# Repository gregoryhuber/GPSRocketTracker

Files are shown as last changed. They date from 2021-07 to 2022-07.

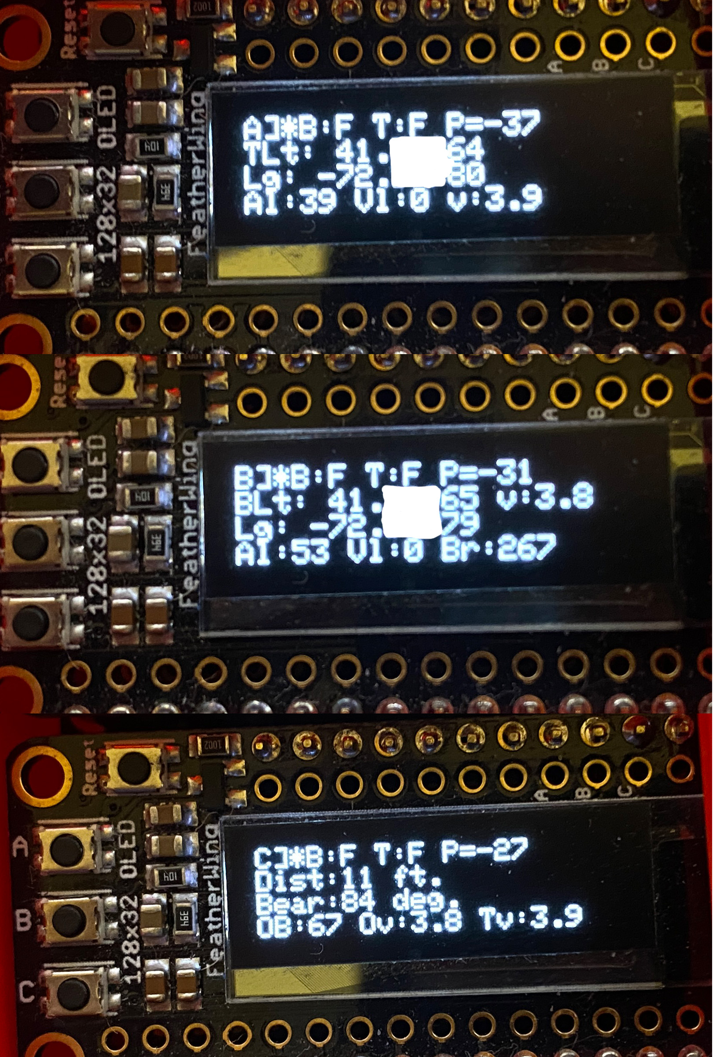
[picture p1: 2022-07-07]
Photos/DisplayScreenExamples.jpg

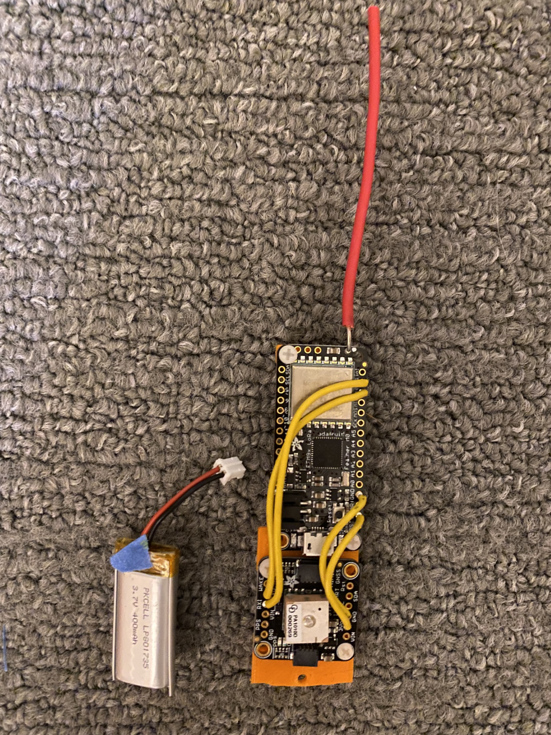
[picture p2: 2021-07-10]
Photos/Transmitter_Front.jpg

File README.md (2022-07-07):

https://github.com/gregoryhuber/GPSRocketTracker

This is the repository for a homebrew GPS Rocket Tracker built around Arduino feather M0 units with embedded LORA radios. Observed successful range over flat territory (when the rocket is laying on the ground) is 1.2km. Longer range has been achieved when the target is airborne, but I'm not sure yet what the maximum is. It likely depends on the antenna.

Comments/improvements/etc. welcome. Please email:

gregory.a.huber@outlook.com with the subject "Arduino Lora Tracker"

==============================

This project requires two units:
(1) A transmitter, the unit that goes in the rocket, which sends its GPS information every second
(2) A receiver/base unit, which you hold onto, which tracks its own GPS location, receives information from the transmitter, and can route you to the transmitter in certain configurations.

Manifest:

Parts lists for each unit, available from AdaFruit, are in the PartsList folder

Shape files (stls) are in the STLfiles folder. There are separate folders for the case that holds the receiver/base unit and transmitter in the two stacked vertical feathers orientation that fits in a 24mm body tube.

Photos of the assembled transmitter and receiver are in the Photos folder.

(Note that there are not photos of the transmitter with an SD Card unit included, but that you can use an SD card on the transmitter.)

Code: 

Recevier.ino in the folder "Receiver" is the code for the receiver/base unit.

Transmitter.ino in the folder "Transmitter" is the code for the transmitter unit.

==============================

Brief overview of code edits/decisions:

The transmitter and receiver need to share a frequency (probably 915mhz, but in the US it can be anything in the range of 902 to 928 MHz if your hardware supports it. See https://www.everythingrf.com/community/lora-frequency-bands-in-north-america) and a 3 digit "MagicNumber." The 3 digit code allows the receiver to know what unit it should be talking to.

See these lines in both files:
#define RF95_FREQ 915.00
#define MagicNumber 123
*** You must set the Mhz and MagicNumber to be the same between your transmitter and receiver units, and should change them from the defaults so you don't conflict with someone else. Even with different codes, units operating on the same frequency may conflict.

You upload the relevant code, using the Arduino IDE, to both the transmitter and the receiver/base unit. 

In the TRANSMITTER codebase, you have to set three flags:

#define UseRadio true
Only turn this to false if you just want to display or capture to the SD Card GPS data0

#define UseSDCardWriter false
You can turn this to true if you install an SD card module and want to record/log data to it.

#define UseDisplay false
Only turn this to true if you have a display installed and you want the transmitter to display its own address.

In the RECEIVER codebase, you have to set two flags

#define UseDisplay true
If you don't have a display (and are only teathered to a PC) you can set to false.

#define PrintDataToSerialForLogging true
This outputs the data received to the serial port, so you can plot it or save it in real time.

PLEASE NOTE: There are also numerous debugging flags in the code, which you can use to diagnose problems (like bad wiring to the GPS or SDCard module/etc.). Leave them as FALSE unless you need to fix things. If you leave them on and try to record data from the receiver on a PC it will screw up the data stream.

==============================

Details about functionality

The receiver has three information screens, selected by pressing the top (A), middle (B), or bottom (C) button on the display.

Screen A displays information about the transmitter.
Screen B displays information about the base station.
Screen C is a navigation screen that guides you from the base to the transmitter.

On all three screens, the top row is the same:

{A,B,C}]*B:XX T:XX P=XX
Where A/B/C is which screen you are on.
The * appears whenever a new packet is received from the transmitter
B: XX indicates the status of the base's GPS fix: F=Valid current Fix;SF(#)=Stale fix, # of seconds since last valid GPS Fix;NF=Never had a valid GPS Fix
T: XX indicates the status of the transmitter's GPS fix: F=Valid current Fix;SF(#)=Stale fix, # of seconds since last valid GPS Fix;NF=Never had a valid GPS Fix;NS Never synced with transmitter
P = XX is the signal strength/RSSI, if synced, of last packed received from transmitter

On Screen A, the next rows will display a summary of the TRANSMITTER's GPS data:
Never Target Sync
or
Never Target Fix + the Transmitter's read battery voltage
or
Lat, Long, Altitude (in meters), Velocity (MPH)+ the Transmitter's read battery voltage

On Screen B, the next rows will display a summary of the BASE's GPS data:
Never Target Fix + the BASE's read battery voltage
or
Lat, Long, Altitude (in meters), Velocity (MPH), Bearing (Degrees) + the Transmitter's read battery voltage

On Screen C, the next rows display
"Can't navigate. Missing something." if either the TRANSMITTER or BASE GPS is missing
or
Distance (feet) and Bearing (degrees) from the BASE to the transmitter
Plus Own bearing, Own Battery Voltage, and Transmitter Battery Voltage

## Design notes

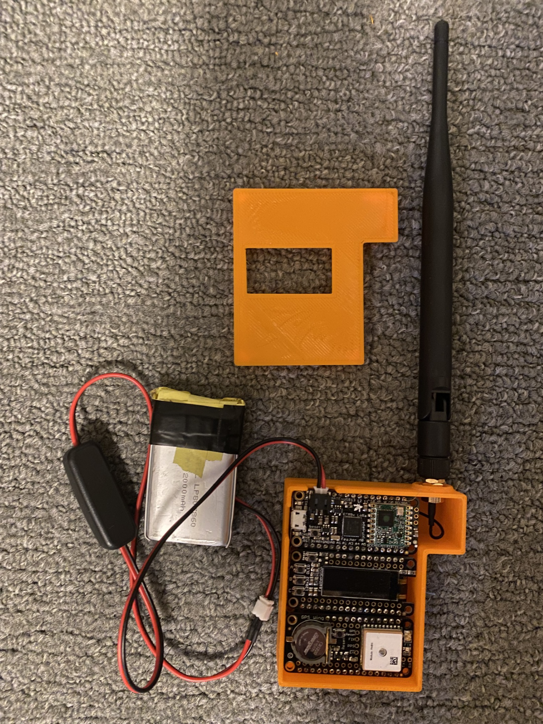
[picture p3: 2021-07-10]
Photos/BaseUnitInCase.jpg

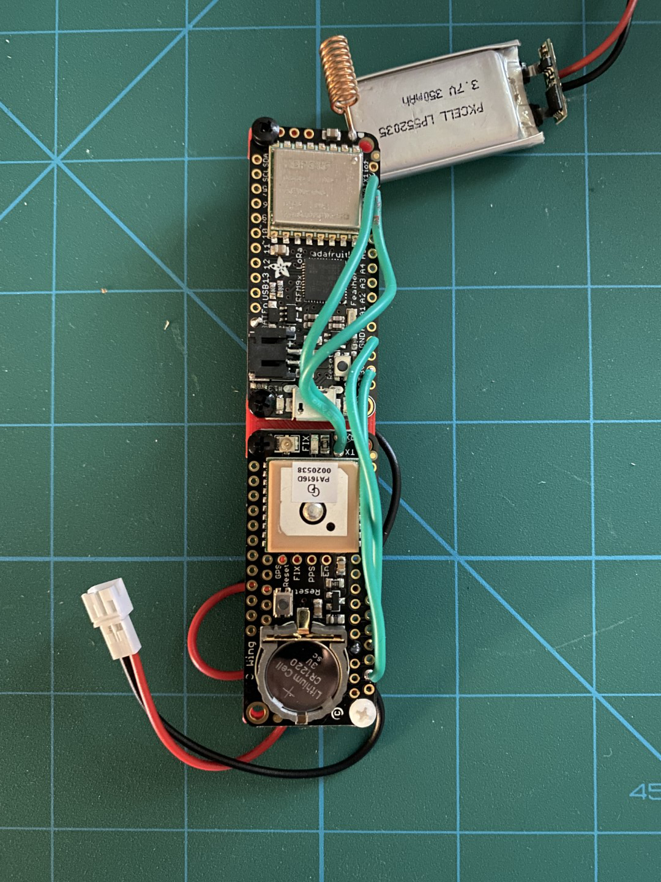
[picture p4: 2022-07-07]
Photos/Transmitter_Narrow_Front.jpg

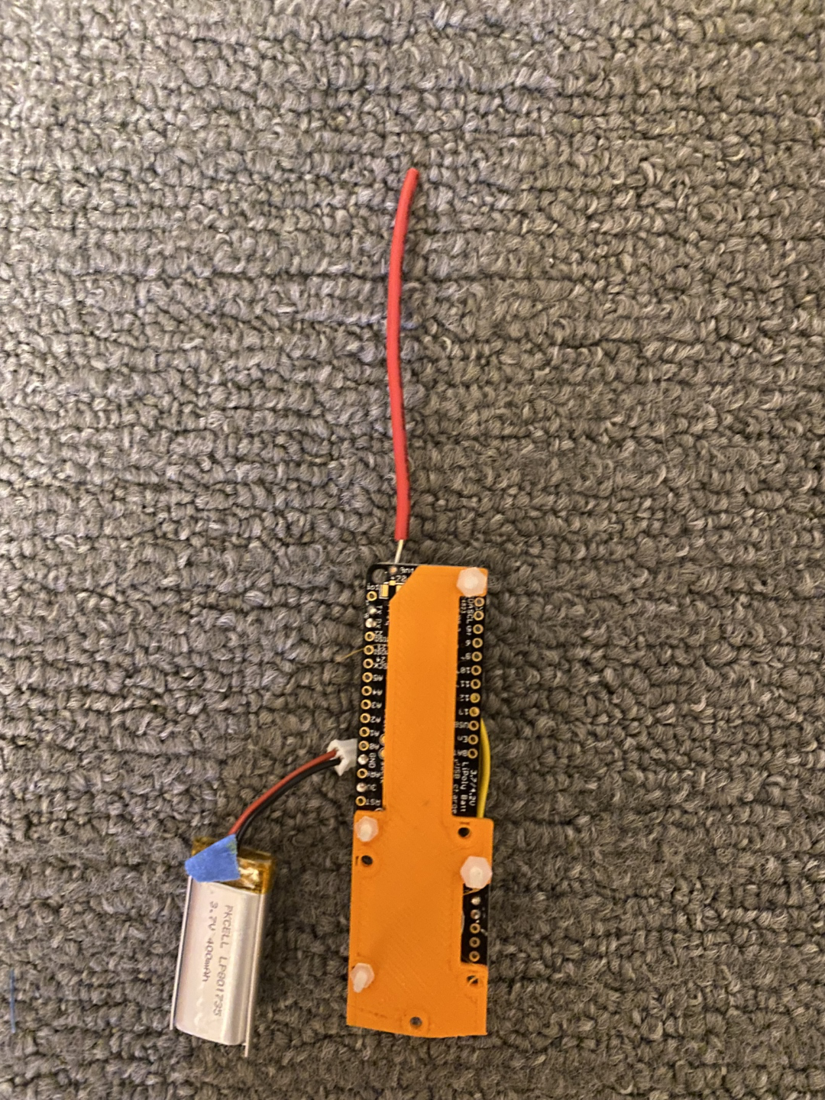
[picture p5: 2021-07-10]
Photos/Transmitter_Rear.jpg

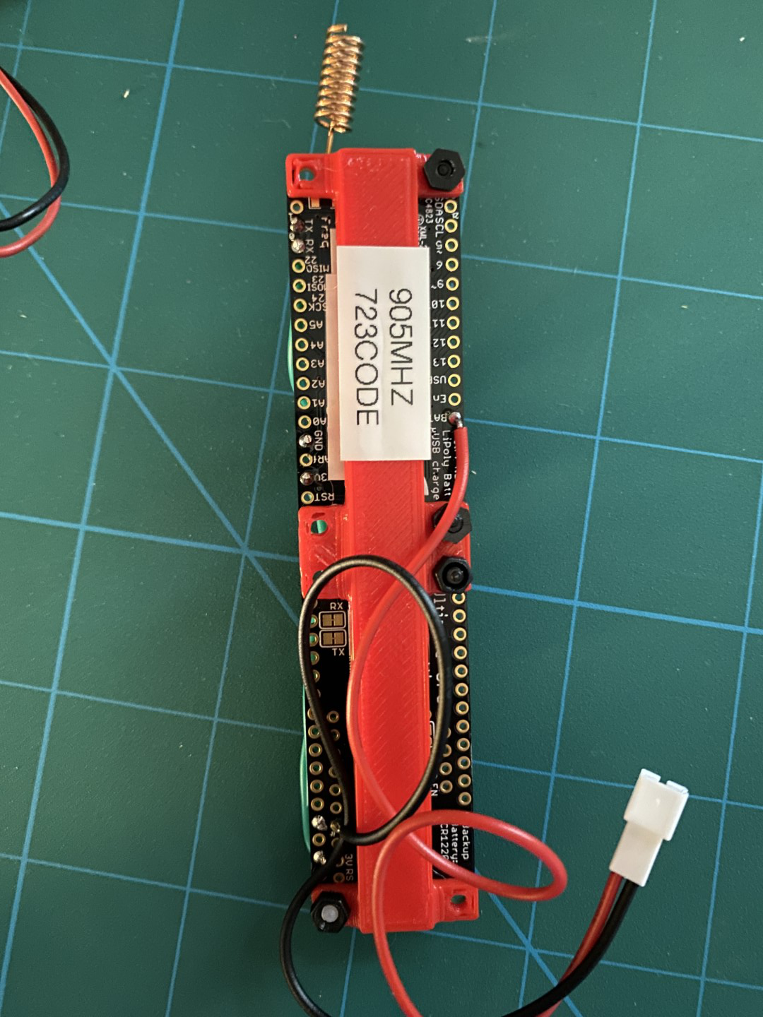
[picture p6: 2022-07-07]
Photos/Transmitter_Narrow_Back.jpg

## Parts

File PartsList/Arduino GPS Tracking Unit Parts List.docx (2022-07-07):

Receiver (Complete Unit with coil antenna $100.25)

FeatherWing Triple (base unit) $8.50

https://www.adafruit.com/product/3417

Adafruit Feather M0 with RFM95 LoRa Radio - 900MHz – RadioFruit $34.95

https://www.adafruit.com/product/3178

Adafruit Featherwing GPS receiver $24.95

https://www.adafruit.com/product/3133

Adafruit Featherwing Display Unit/Control Buttons (with headers) $15.95

https://www.adafruit.com/product/3045

Large battery $14.95

https://www.adafruit.com/product/328

Antenna Options:

Simple Spring (coil) Antenna $.95

https://www.adafruit.com/product/4269

OR

uFL SMT Connector $.75

https://www.adafruit.com/product/1661

900 Mhz Antenna $12.75

https://www.adafruit.com/product/3340

Optional:

Battery patch cable with switch $2.95

https://www.adafruit.com/product/3064

3D Printed Case for Base Unit

With Spring Antenna:

With large antenna:

See BaseUnitBottomOfCase.stl and BaseUnitTopOfCase.stl

Transmitting Unit ($66.85)

Adafruit Feather M0 with RFM95 LoRa Radio - 900MHz – RadioFruit $34.95

https://www.adafruit.com/product/3178

GPS receiver

Option 1, smaller: $29.95

https://www.adafruit.com/product/746

Option 2, feather: $24.95

https://www.adafruit.com/product/3133

400mah LIPO battery $6.95

https://www.adafruit.com/product/3898

Quarter Wavelength Wire antenna (3.12inches) (free)

http://www.csgnetwork.com/antennagenericfreqlencalc.html

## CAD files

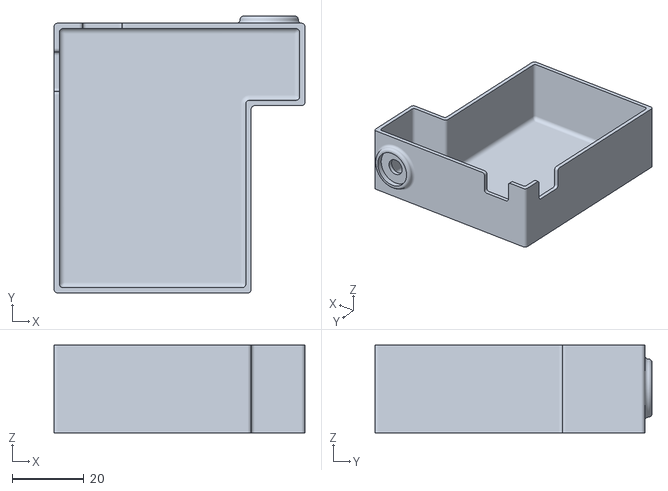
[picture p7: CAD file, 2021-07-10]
STLFiles/BaseUnitCase/BaseUnitBottomOfCase.stl
70.0 x 77.2 x 24.5

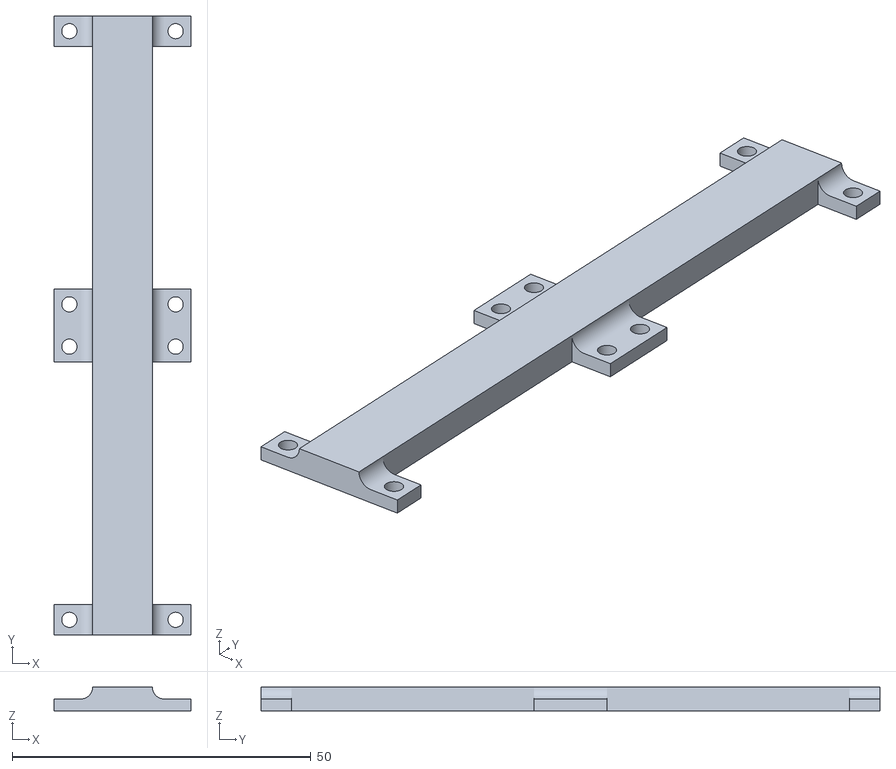
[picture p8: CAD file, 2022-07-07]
STLFiles/VerticalFeathers24MMTube/VerticalFeathers24MMTube.stl
22.9 x 103.6 x 4.00

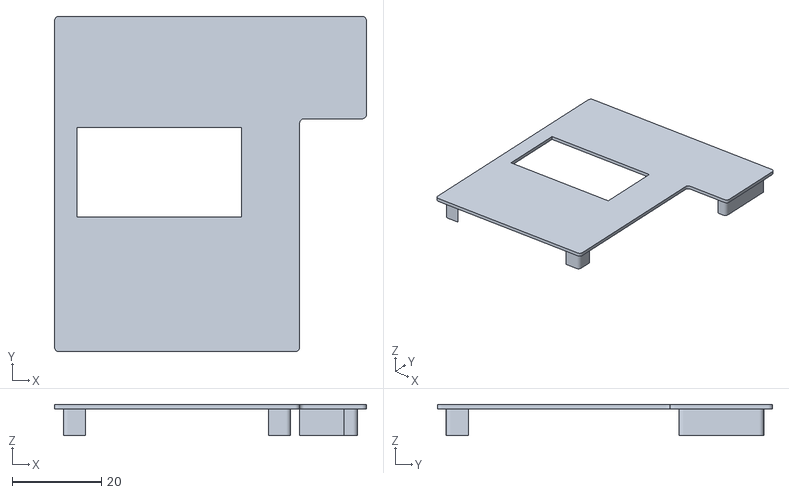
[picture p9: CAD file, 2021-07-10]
STLFiles/BaseUnitCase/BaseUnitTopOfCase.stl
70.0 x 75.2 x 7.00

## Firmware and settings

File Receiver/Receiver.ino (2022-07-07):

//////////////////////////////////////////////////////////////////////////
// RFM95 Lora Arduino GPS tracking system
// Version 2.1
// 2022/07/01
// Gregory Huber (gregory.a.huber@outlook.com)
//
// This is the code for the RECEIVER
//
//////////////////////////////////////////////////////////////////////////

// This is the receiver half of the codebase for an Arduino feather-based GPS tracking system suitable for rocket tracking
// The physical setup is comprised of a base station (receiver) and a tracker (transmitter)

// The base station is built around the following minimal equipment:
// Adafruit Feather M0 with RFM95 LoRa Radio - 900MHz – RadioFruit https://www.adafruit.com/product/3178

// The following parts are optional if you just want to capture data from the transmitter directly to a PC

// Necessary to dispay incoming GPS data and to use free navigation (without connection to a PC)
// Feather Display Unit/Control Buttons (with headers) https://www.adafruit.com/product/3045
// Set UseDisplay below to true to use

// Necessary to use free navigation (without connection to a PC)
// Feather GPS receiver https://www.adafruit.com/product/3133
// Even if no GPS is present, code will still run

// These are hardware options to hold everything as well as a good antenna option. I find soldering the uFL connector hard so I tend to use simple wire antennas
// FeatherWing Triple (base unit) https://www.adafruit.com/product/3417  
// uFL SMT Connector https://www.adafruit.com/product/1661
// 900 Mhz Antenna https://www.adafruit.com/product/3340
// 2000mAh LIPO battery https://www.adafruit.com/product/2011

// This code draws on the following resouces and references. Thank you.
// This is a fully fleshed out example from which many of the transmission details were copied https://github.com/mloudon/electrosew/blob/master/feather_send/feather_send.ino
// https://gis.stackexchange.com/questions/252672/calculate-bearing-between-two-decimal-gps-coordinates-arduino-c
// https://community.particle.io/t/tinygps-using-distancebetween/28233/3
// http://www.airspayce.com/mikem/arduino/RadioHead/classRH__RF95.html
// https://www.thethingsnetwork.org/forum/t/best-practices-when-sending-gps-location-data/1242/40

// Version 2.5 (2022/07):
// Introduced data structures, which allowed much more efficiently sending more data in the LORA packet
// On the transmitter:
    // Read and send battery voltage
    // Added support for a data logger
    // Refined display code to fix what is displayed on transmitter
// On the receiver/base unit:
    // Implement serial logging to connect to PC
    // Improve option for running without display
    // Read and display battery voltages
    // Improved handling of stale packets/stale GPS data
    // More data/info now displayed on screen

#include <Adafruit_GPS.h>
#include <math.h>;
#include <SPI.h>
#include <Wire.h>
#include <Adafruit_GFX.h>
#include <Adafruit_SSD1306.h>
#include <RH_RF95.h>

////////////////////////////////////////////////////////////////////////////////////////////
//
// Radio constants
//
////////////////////////////////////////////////////////////////////////////////////////////
  
  // This is important. This defines the frequency the units will use. Both base and transmitter need to be on the same frequency
  // LORA frequency range in the US is 902 to 928 MHz https://www.everythingrf.com/community/lora-frequency-bands-in-north-america
  // I do not not know if you can provide more specificity here (say 915.2)
  #define RF95_FREQ 915
  
  // The magic number is a unique three digit code that is used to verify the pair between tracker and base unit.
  // Valid ranges are 000 to 999
  // If these numbers don't match, any incoming packet is ignored
  // Please change it to something different form this so that your tracker doesn't conflict with someone else's!
  #define MagicNumber 123

////////////////////////////////////////////////////////////////////////////////////////////
//
// Hardware setup options
//
////////////////////////////////////////////////////////////////////////////////////////////

  #define UseDisplay true

////////////////////////////////////////////////////////////////////////////////////////////
//
// Connection to PC options
//
////////////////////////////////////////////////////////////////////////////////////////////

  // For real time-tracking using PC, enable printing of target GPS to serial port for plotting
  #define PrintDataToSerialForLogging true
  // Note that if this is enabled, other debugging flags below should be set to false 
  // or else reading serial port will likely crash

////////////////////////////////////////////////////////////////////////////////////////////
//
// Timing constants
//
////////////////////////////////////////////////////////////////////////////////////////////

  // Update intervals for getting own GPS locations
  // These are in milliseconds, so 1000 = 1 second
  #define OwnGPSUpdateInterval 500
  #define DisplayUpdateInterval 250
  #define ButtonUpdateInterval 500
  #define SerialPortUpdateInterval 500

////////////////////////////////////////////////////////////////////////////////////////////
//
// Debugging
//
////////////////////////////////////////////////////////////////////////////////////////////

  // Enable each of these flags to enable diffent parts of the DebugDebugging code
  #define DebuggingOwnGPS false        // DebuggingOwnGPS prints to serial own gps data
  #define DebuggingIncoming false      // DebuggingIncoming prints to serial the incoming packet data
  #define DebuggingOwnRadio false      // DebuggingOwnRadio prints to serial configuration for the LORA radio

  // Fake data used for static GPS testing
  // Lat/Long is the New Haven, CT Green. Other data is made up.
  #define UseStaticData false
  #define StaticLat 41.308231
  #define StaticLong -72.926173
  #define StaticBearing 317
  #define StaticVelocity 987
  #define StaticAlt 3611
  #define StaticNumSatelites 8
  #define StaticSecondsSinceUpdate 27
  #define StaticEverValidFix 1
  #define StaticVBAT 4.10  

////////////////////////////////////////////////////////////////////////////////////////////
//
// Define pins/hardware
//
////////////////////////////////////////////////////////////////////////////////////////////

  //////////////////////////////////////////////////////////////////////////////////////////
  // Battery voltage
  // Battery voltage is measured on A7 on the M0
  #define VBATPIN A7

  //////////////////////////////////////////////////////////////////////////////////////////
  // GPS
  // hardware serial port for the GPS
  #define GPSSerial Serial1

  // Connect to the GPS on the hardware port
  Adafruit_GPS GPS(&GPSSerial);

  //////////////////////////////////////////////////////////
  // Setup OLED display
  Adafruit_SSD1306 display = Adafruit_SSD1306(128, 32, &Wire);
      
  // OLED FeatherWing buttons map to different pins depending on board:
  #define BUTTON_A  9
  #define BUTTON_B  6
  #define BUTTON_C  5

  //////////////////////////////////////////////////////////////////////////////////////////
  // Setup LORA Radio
  #define LED           13
  #define RFM95_CS      8
  #define RFM95_INT     3
  #define RFM95_RST     4

  // Create singleton instance of the radio driver
  RH_RF95 rf95(RFM95_CS, RFM95_INT);

////////////////////////////////////////////////////////////////////////////////////////////
//
// Structures
//
////////////////////////////////////////////////////////////////////////////////////////////

  // uint8_t is 0 to 255
  // uint16_t is 0 to 65535 
  // uint32_t 0 to 4,294,967,295
  
  // This is the structure we use to store our own GPS data at all times
  struct __attribute__ ((packed)) processed_gps_t {
    bool evervalidfix;              // whether we've ever had a valid gps fix
    uint32_t lastupdatemillis;      // last gps update in millis format
    uint32_t lastupdatetime;        // last gps update in hhmmss integer format
    uint32_t secondsincelastupdate; // last gps update in millis format
    bool stalelocation;             // whether last gps update was more than 60 seconds ago (1=yes)
    
    int numsatellites;              // number of satellites in last fix
  
    double latitude;          // in decimal format
    double longitude;         // in decimal format
    int32_t altitude_meters;  // in meters
    uint32_t velocity_mph;    // in mph
    uint16_t  bearing;        // in degrees (0-360)
    
    double bvolt;             // battery voltage [Range 3.0 to 4.2]
  } ;
  
  // declaring a new type "radiopacket_gps_t" as a structure for the info we want to send/receive
  // there is a fair bit of being creative here to keep the packet as small as is possible
  struct __attribute__ ((packed)) radiopacket_gps_t {
  
    //This is 2-bit unsigned integer, which ranges from 0 to 65535 
    uint16_t vbat_code;               // 2 digits are vbat * 10 and 3 digits are unique code for pairing
    
    //Thse are 4-bit unsigned integers, which ranges in value from 0 to 4,294,967,295 = 10 digits to play with
    //With 5 digits of decimal precision we still have two additional place for storing other data
    uint32_t bear_veloc_alt;          // format is XXX bearing, XXX velocity capped at 999, and XXXX altitude in meters +100 capped at 9999
    uint32_t latitude_sats_ever;      // lat with +180 to ensure positive and 5 digits precision uses 8 digits, 1 digit for # satellites seen, 1 digit for whether ever valid fix
    uint32_t longitude_sincelastfix;  // long with +180 to ensure positive and 5 digits precision uses 8 digits, 2 digits for seconds since last fix, capped at 99
  } ;
  
////////////////////////////////////////////////////////////////////////////////////////////
//
// Globabl Variables
//
////////////////////////////////////////////////////////////////////////////////////////////

  // Own GPS Data
  processed_gps_t OwnGPSData = {
    .evervalidfix=0,
    .lastupdatemillis=0,
    .lastupdatetime=0,
    .secondsincelastupdate=0,
    .stalelocation=0,
    .numsatellites=0,
    .latitude=0,
    .longitude=0,
    .altitude_meters=0,
    .velocity_mph=0,
    .bearing=0,
    .bvolt=0
  };

  // Own GPS Data
  processed_gps_t TargetGPSData = {
    .evervalidfix=0,
    .lastupdatemillis=0,
    .lastupdatetime=0,
    .secondsincelastupdate=0,
    .stalelocation=0,
    .numsatellites=0,
    .latitude=0,
    .longitude=0,
    .altitude_meters=0,
    .velocity_mph=0,
    .bearing=0,
    .bvolt=0
  };

  // Radio packet to receive
  radiopacket_gps_t SentDataToProcess;

  // Whether a new valid GPS location has arrived that needs to be parsed/stored
  boolean NewValidGPSDataArrived = 0;
  boolean BaseEverValidGPS = 0;  

  // Information about Target
  boolean TargetEverSync = 0;
  boolean TargetEverValidGPS = 0;  
  boolean TargetStaleLocation = 0;
  boolean GotNewLoraPacket = 0;
  boolean DisplayNewPacketFlag = 0;
  uint16_t SecondsSinceIncomingPacket = 0;
  uint16_t SecondsSinceIncomingGPS = 0;
  
  // Last RSSI from radio
  int lastRSSI;

  // store last button pushed on diplay, default to 'A'
  char LastButtonPushed = 'A';

  // Counter for packets in logfile

  // Timers
  uint32_t LastFixFromOwnGPS = 0;         // Last millis for which we got a Valid GPS Fix
  uint32_t LastUpdateOwnGPSPacket = 0;    // Last millis at which we updated the GPS Packet
  uint32_t LastLoraPacket = 0;            // Last millis for which we got a Valid GPS Fix
  uint32_t LastDisplayUpdate = 0;         // Last millis at which display was updated.
  uint32_t LastButtonUpdate = 0;          // Last millis at which button status was updated.
  uint32_t LastSerialPortUpdate = 0;      // Last millis at which sent logging packet to serial port.
  uint32_t EndLoopMillis = 0;             // Last millis at which we finished the main loop.
                                          // Used solely to deal with looping in Millis.
 
////////////////////////////////////////////////////////////////////////////////////////////
////////////////////////////////////////////////////////////////////////////////////////////
////////////////////////////////////////////////////////////////////////////////////////////
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
void loop() {

  //////////////////////////////////////////////////////////////////////////
  // Each time through the loop, check for a LORA packet
  //
  
  // Turn on communication to LORA. Keeping it off the rest of the time stops this from interfering with other parts of code.
  digitalWrite (RFM95_CS, LOW);
  
  if (rf95.available()) {
    GotNewLoraPacket = receiveLoraPacket();
    if (GotNewLoraPacket) {
      TargetEverSync = true;
      if (TargetGPSData.evervalidfix==1) {
        TargetEverValidGPS = true;
      }
      lastRSSI = rf95.lastRssi();
      LastLoraPacket=millis();
      DisplayNewPacketFlag=true;
    }
  }
  
  // Turn off communication to LORA. Keeping it off stops this from interfering with other parts of code.
  digitalWrite (RFM95_CS, HIGH);

  //////////////////////////////////////////////////////////////////////////
  // Each time through the loop, attempt to read GPS data.
  // This code doesn't try to read from GPS unless it is available.
  // Additionally, if no new data is available, it just skips through.
  if (GPSSerial.available() > 0) {
    char c = GPS.read();
    if (GPS.newNMEAreceived()) {
      if (GPS.parse(GPS.lastNMEA())) {
        if (GPS.fix==1) {
          NewValidGPSDataArrived = 1;
          BaseEverValidGPS = 1;
          LastFixFromOwnGPS = millis();
        }
      }
    }
  }

  //////////////////////////////////////////////////////////////////////////
  // Update Own GPS calculations every OwnGPSUpdateInterval
  if ((LastUpdateOwnGPSPacket+OwnGPSUpdateInterval )<millis()) {
    LastUpdateOwnGPSPacket=millis();

    // This block of conditional code just sets the GPS data to either the fixed stata data for testing purposes or the actual GPS data
    if (UseStaticData) {
      // Fixed data for testing purpuses
      OwnGPSData.evervalidfix=StaticEverValidFix;
      OwnGPSData.lastupdatemillis=millis();
      OwnGPSData.lastupdatetime=234233;
      OwnGPSData.secondsincelastupdate=(OwnGPSData.lastupdatemillis-(millis()-(1000*StaticSecondsSinceUpdate)))/1000;
      OwnGPSData.stalelocation=(OwnGPSData.secondsincelastupdate>60);
      OwnGPSData.numsatellites=StaticNumSatelites;
      OwnGPSData.latitude=StaticLat;
      OwnGPSData.longitude=StaticLong;
      OwnGPSData.altitude_meters=StaticAlt;
      OwnGPSData.velocity_mph=StaticVelocity;
      OwnGPSData.bearing=StaticBearing;
      OwnGPSData.bvolt = StaticVBAT;
    }
    else {
      // Actual data
      OwnGPSData.bvolt = (2*3.3*analogRead(VBATPIN))/1024;
      //OwnGPSData.bvolt = 4.2;
      // NewValidGPSDataArrived: This flag lets us know if in the intervening period a new GPS packet with a valid fix has been parsed
      if (NewValidGPSDataArrived) {
        // Do this if new data has arrived
        NewValidGPSDataArrived = 0;
        OwnGPSData.evervalidfix=1;
        OwnGPSData.lastupdatemillis=LastFixFromOwnGPS;
        OwnGPSData.lastupdatetime=GPS.hour*10000+GPS.minute*100+GPS.seconds;
        OwnGPSData.secondsincelastupdate=0;
        OwnGPSData.numsatellites=(int)GPS.satellites;
        OwnGPSData.latitude=GPS.latitudeDegrees;
        OwnGPSData.longitude=GPS.longitudeDegrees;
        OwnGPSData.altitude_meters=GPS.altitude;
        OwnGPSData.velocity_mph=GPS.speed*1.15078;
        OwnGPSData.bearing=(int)GPS.angle;
        OwnGPSData.stalelocation=0;
      }
      else {
        // Do this if new data has NOT arrived
        OwnGPSData.secondsincelastupdate=(millis()-LastFixFromOwnGPS)/1000;
        OwnGPSData.stalelocation=(OwnGPSData.secondsincelastupdate>60);
        if (OwnGPSData.stalelocation) {
          OwnGPSData.numsatellites=0;
        }
      }
      
    }

    if (DebuggingOwnGPS) {
      Serial.print("\nDebugging Own GPS-> ");
      Serial.print("Vbat: ");
      Serial.print(OwnGPSData.bvolt);
      Serial.print(" Magic Number: ");
      Serial.println(MagicNumber);
      
      Serial.print("Bearing: ");
      Serial.print(OwnGPSData.bearing);
      Serial.print(" Velocity: ");
      Serial.print(OwnGPSData.velocity_mph);
      Serial.print(" Altitude: ");
      Serial.println(OwnGPSData.altitude_meters);
      
      Serial.print("Latitude: ");
      Serial.print(OwnGPSData.latitude, 6);
      Serial.print(" Longitude: ");
      Serial.println(OwnGPSData.longitude, 6);
      
      Serial.print("Ever Fix: ");
      Serial.print(OwnGPSData.evervalidfix);
      Serial.print(" #Satelites: ");
      Serial.print(OwnGPSData.numsatellites);
      Serial.print(" Seconds since update: ");
      Serial.println(OwnGPSData.secondsincelastupdate);
    }
  }

  //Serial.print("Old button: ");
  //Serial.println(LastButtonPushed);
  //Serial.print("Button reads: A:");
  //Serial.print(analogRead(BUTTON_A));
  //Serial.print(" B: ");
  //Serial.print(digitalRead(BUTTON_B));
  //Serial.print(" C: ");
  //Serial.println(digitalRead(BUTTON_C));

  //////////////////////////////////////////////////////////////////////////
  // Query Button Status every ButtonUpdateInterval
  if ((LastButtonUpdate+ButtonUpdateInterval)<millis() & UseDisplay) {

    LastButtonUpdate=millis();
       
    // Record which button is being pushed. Note if multiple buttons, records C
    if(!digitalRead(BUTTON_C)) {
      LastButtonPushed = 'C';
    }
    else if(!digitalRead(BUTTON_B)) {
      LastButtonPushed = 'B';
    }
    else if(analogRead(BUTTON_A)<100) {
      // Note: The analog read is because when reading battery voltage, this digital read is no longer reliable.
      // So instead of using digitalRead, setting a specific threshold with analogRead
      LastButtonPushed = 'A';
    }
  }

  //Serial.print("New button: ");
  //Serial.println(LastButtonPushed);
  //delay(1000);
  
  //////////////////////////////////////////////////////////////////////////
  // Update OLED display screen every ButtonUpdateInterval
  if ((LastDisplayUpdate+DisplayUpdateInterval )<millis()) {

    LastDisplayUpdate=millis();

    // To lessen computational load, we only make these calculations when relevant, which is inside of display update loop
    if(TargetEverSync) {
      SecondsSinceIncomingPacket = int((millis()-LastLoraPacket)/1000);
      if(TargetEverValidGPS) {  
        SecondsSinceIncomingGPS = SecondsSinceIncomingPacket + TargetGPSData.secondsincelastupdate;
        if(SecondsSinceIncomingGPS>60) {
          TargetStaleLocation=1;
          } else {
          TargetStaleLocation=0; 
          }
      }
    }
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

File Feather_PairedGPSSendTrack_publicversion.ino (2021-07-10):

//////////////////////////////////////////////////////////////////////////
// RFM95 Lora Arduino GPS tracking system
// Version 1.1
// 2021/07/10
// Gregory Huber (gregory.a.huber@outlook.com)
//////////////////////////////////////////////////////////////////////////

// This is the codebase for an Arduino feather-based GPS tracking system suitable for rocket tracking
// The physical unit is comprised of a base station and a tracker (transmitter)
// The codebase for both components is the same. You set below whether this is a tracker (ReceiveNotTransmitLocation FALSE) or a receiver (ReceiveNotTransmitLocation TRUE)
// For the tracker/transmitter, the display unit is optional, configured using UseDisplay

// The base station is built around the following minimal equipment:
// Adafruit Feather M0 with RFM95 LoRa Radio - 900MHz – RadioFruit https://www.adafruit.com/product/3178
// Feather GPS receiver https://www.adafruit.com/product/3133
// Feather Display Unit/Control Buttons (with headers) https://www.adafruit.com/product/3045
// FeatherWing Triple (base unit) https://www.adafruit.com/product/3417  
// uFL SMT Connector https://www.adafruit.com/product/1661
// 900 Mhz Antenna https://www.adafruit.com/product/3340

// The (smallest) tracking unit is built around an the following equipment:
// Adafruit Feather M0 with RFM95 LoRa Radio - 900MHz – RadioFruit https://www.adafruit.com/product/3178
// GPS receiver https://www.adafruit.com/product/746
// 400mah LIPO battery https://www.adafruit.com/product/3898
// Quarter Wavelength Wire antenna (3.12inches) http://www.csgnetwork.com/antennagenericfreqlencalc.html

// This code draws on the following resouces and references. Thank you!
// This is a fully fleshed out example from which many of the transmission details were copied https://github.com/mloudon/electrosew/blob/master/feather_send/feather_send.ino
// https://gis.stackexchange.com/questions/252672/calculate-bearing-between-two-decimal-gps-coordinates-arduino-c
// https://community.particle.io/t/tinygps-using-distancebetween/28233/3
// http://www.airspayce.com/mikem/arduino/RadioHead/classRH__RF95.html
// https://www.thethingsnetwork.org/forum/t/best-practices-when-sending-gps-location-data/1242/40

#include <Adafruit_GPS.h>
#include <math.h>;
#include <SPI.h>
#include <Wire.h>
#include <Adafruit_GFX.h>
#include <Adafruit_SSD1306.h>
#include <RH_RF95.h>

//////////////////////////////////////////////////////////
// Specify mode and hardware

// Set to true to enable display. Set to false to disable. 
// It doesn't make sense for the base unit not to have a display (you couldn't see what data you were getting). It is optional for the tracker
#define UseDisplay false
// Set this to false to make it a transmitter, to true to be receiver
#define ReceiveNotTransmitLocation false

//////////////////////////////////////////////////////////
// DebugDebugging mode
// Enable each of these flags to enable diffent parts of the DebugDebugging code
#define DebuggingButtons false
#define DebuggingDisplay false
#define DebuggingOwnGPS false
#define DebuggingTargetGPS false
#define DebuggingRadio false

//////////////////////////////////////////////////////////
// Read battery voltage
// For reasons I don't understand, reading the battery voltage causes the remaining code to fail. It is disabled below.
#define VBATPIN A7

//////////////////////////////////////////////////////////
// Setup GPS

// what's the name of the hardware serial port for the GPS?
#define GPSSerial Serial1

// Connect to the GPS on the hardware port
Adafruit_GPS GPS(&GPSSerial);

//////////////////////////////////////////////////////////
// Setup OLED display

Adafruit_SSD1306 display = Adafruit_SSD1306(128, 32, &Wire);
  
// OLED FeatherWing buttons map to different pins depending on board:
#define BUTTON_A  9
#define BUTTON_B  6
#define BUTTON_C  5

//////////////////////////////////////////////////////////
// Setup LORA Radio
#define LED 13

#define RFM95_CS      8
#define RFM95_INT     3
#define RFM95_RST     4

// This is important. This defines the frequency the units will use. Both base and transmitter need to be on the same frequency
// I do not not know if you can provide more specificity here (say 915.2)
#define RF95_FREQ 915.0

// The magic number is a unique two digit code that is used to verify the pair between tracker and base unit
// Please change it to something different form this so that your tracker doesn't conflict with someone else's!
#define MAGIC_NUMBER_LEN 2
// Magic numbers are two hex digits; I've set this to 2,13 for now, but change it to something else!
const uint8_t MAGIC_NUMBER[MAGIC_NUMBER_LEN] = {0x02, 0x0D};

// Singleton instance of the radio driver
RH_RF95 rf95(RFM95_CS, RFM95_INT);

//////////////////////////////////////////////////////////
// set update intervals for getting own and target GPS locations and displaying to OLED
// These are in milliseconds, so 1000 = 1 second
#define OwnGPSUpdateInterval 1000
#define TargetGPSUpdateInterval 1000
#define DisplayUpdateInterval 750
#define ButtonUpdateInterval 500
#define SendViaRadioInterval 1000

// for target GPS, either grab via radio or set to fixed static location for testing purposes
#define TargetGPSUseStatic false
// New Haven Green
#define TargetStaticLat 41.308200 
#define TargetStaticLong -72.926100
#define TargetStaticAlt 100

// Whether ever received a valid GPS fix
bool OwnEverValidGPS = false;
bool TargetEverSync = false;
bool TargetEverValidGPS = false;

// Timers used to figure out last target GPS update, last local GPS update, and Last display
uint32_t LastOwnLocationUpdate = millis();
uint32_t LastTargetLocationUpdate= millis();
uint32_t LastDisplayUpdate = millis();
uint32_t LastButtonUpdate = millis();
uint32_t LastSendViaRadio = millis();

double OwnLat, OwnLong;
int OwnGSPLastQuality, OwnAlt, OwnSpeed, OwnBearing;
uint32_t OwnLastUpdateMillis, OwnLastUpdateTime;
bool OwnStaleLocation = false;

double TargetLat, TargetLong;
int TargetAlt;
uint32_t TargetLastUpdateMillis, TargetLastUpdateTime;
bool TargetStaleLocation = false;
bool DisplayNewPacketFlag = false;
bool SendingPacket = false;

// store last button pushed on diplay, default to 'B'
char LastButtonPushed = 'B';
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

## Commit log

2021-07-10 Initial Push.
    [BaseUnitBottomOfCase.stl, BaseUnitTopOfCase.stl]
2022-07-07 Mega Release
    [BaseUnitBottomOfCase.stl, BaseUnitTopOfCase.stl, VerticalFeathers24MMTube.stl]
